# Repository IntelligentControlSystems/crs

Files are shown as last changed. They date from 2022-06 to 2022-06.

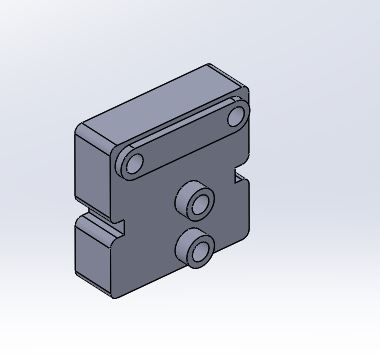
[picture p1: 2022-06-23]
3D_printed_files/miniz_awd/bottom_bracket/Bottom.JPG

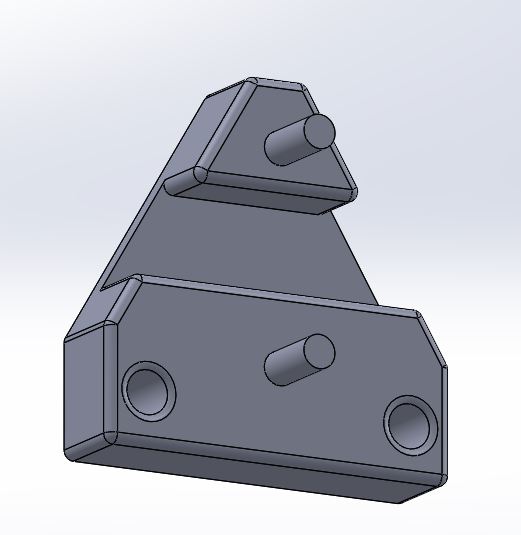
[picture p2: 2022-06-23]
3D_printed_files/assembly_tools/Alignment tool.JPG

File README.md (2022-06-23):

# Collaborative Robotic Systems - CRS


Robotics platform to test control, estimation, and learning algorithms. 

## General 
Collaborative Robotic Systems (CRS) is a flexible and open source hardware and software framework for simulating and testing autonomous racing, autonomous driving, and multi-agent control. This branch contains the hardware design (PCBs, gerber files, BoM, etc).

More information can be found [here](https://idsc.ethz.ch/research-zeilinger/research-projects/demonstrators.html). 

## Contacts
For more information contact [Andrea Carron](https://idsc.ethz.ch/research-zeilinger/research-projects/demonstrators.html)

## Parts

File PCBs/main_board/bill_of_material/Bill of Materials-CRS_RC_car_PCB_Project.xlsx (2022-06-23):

Comment | Description | Designator | Footprint | LibRef | Manufacturer | Manufacturer Part Number | Note | Quantity | Supplier | Supplier Part Number | Library Reference | Manufacturer 1 | Manufacturer Part Number 1 | Supplier 1 | Supplier Part Number 1
22uF | capacitor | C1, C2, C8, C9 | CAP_0603i_1608m -N | Cap |  |  |  | 4 |  |  | Cap |  |  | Digi-Key | 1276-7076-1-ND
2u2F | capacitor | C3, C10 | CAP_0603i_1608m -N | Cap |  |  |  | 2 |  |  | Cap
1nF | capacitor | C4, C13 | CAP_0603i_1608m -N | Cap |  |  |  | 2 |  |  | Cap |  |  | Digi-Key | 478-1215-1-ND
22nF | capacitor | C5, C6, C7, C11, C12, C14 | CAP_0603i_1608m -N | Cap |  |  |  | 6 |  |  | Cap |  |  | Digi-Key | 490-4782-1-ND
0.1uF | capacitor | C15, C18, C20, C21, C34, C35, C39, C41, C42, C51 | CAP_0603i_1608m -N | Cap |  |  |  | 10 |  |  | Cap |  |  | Digi-Key | 1276-1006-1-ND
10nF | capacitor | C16, C36, C38, C47, C48, C49, C50 | CAP_0603i_1608m -N | Cap |  |  |  | 7 |  |  | Cap |  |  | Digi-Key | 399-10040-1-ND
10uF | capacitor | C17, C29 | CAP_0603i_1608m -N | Cap |  |  |  | 2 |  |  | Cap |  |  | Digi-Key | 490-3896-1-ND
1uF | capacitor | C19, C24, C26, C28, C30, C40, C43, C44, C45, C46 | CAP_0603i_1608m -N | Cap |  |  |  | 10 |  |  | Cap |  |  | [NoParam], Digi-Key | [NoParam], 445-1604-1-ND
680pF | capacitor | C22 | CAP_0603i_1608m -N | Cap |  |  |  | 1 |  |  | Cap |  |  | Digi-Key | 478-06035C681JAT2ACT-ND
47uF | capacitor | C23, C31 | CAP_1210i_3225m -N | Cap |  |  |  | 2 |  |  | Cap |  |  | Digi-Key | 490-6538-1-ND
47pF | capacitor | C25, C37 | CAP_0603i_1608m -N | Cap |  |  |  | 2 |  |  | Cap |  |  | Digi-Key | 478-12725-1-ND
10pF | capacitor | C27 | CAP_0603i_1608m -N | Cap |  |  |  | 1 |  |  | Cap |  |  | Digi-Key | 478-1163-1-ND
4.7uF | capacitor | C32, C33 | CAP_0603i_1608m -N | Cap |  |  |  | 2 |  |  | Cap |  |  | Digi-Key | 445-14258-1-ND
4.3nF | capacitor | C52, C53 | CAP_0603i_1608m -N | Cap |  |  |  | 2 |  |  | Cap |  |  | Digi-Key | 311-3858-1-ND
Diode Tranzorb | Transient Voltage Suppression (TVS) Diode | D1 | Diode SMB DO-214aa -N | Diode Tranzorb |  |  |  | 1 |  |  | Diode Tranzorb |  |  | Digi-Key | SMBJ16CALFCT-ND
BZX84J-B12,115 | Schottky Diode | D2, D3, D4, D8 | SOD-323F | Diode Schottky |  |  |  | 4 |  |  | Diode Schottky |  |  | Digi-Key, [NoParam] | 1727-6256-1-ND, [NoParam]
 | LED | D5, D6, D7 | LED_0603i_1608m-n | Diode LED |  |  |  | 3 |  |  | Diode LED
BMI088 Shuttle board 3.0 | Bosch Sensortec BMI088 shuttle board 1.27MM pitch | IC1 | BMI088 Shuttle board 3.0 - SM | BMI088 Shuttle board 3.0 |  |  |  | 1 |  |  | BMI088 Shuttle board 3.0 |  |  | Mouser | 262-SB3.0BMI088
ESP32-WROOM-32D |  | IC2 | ESP32-WROOM-32D | ESP32-WROOM-32D |  |  |  | 1 |  |  | ESP32-WROOM-32D |  |  | Digi-Key | 1904-1023-1-ND
Inductor | Inductor | L1 | Würth 744311470 | Inductor |  |  |  | 1 |  |  | Inductor |  |  | Digi-Key | 732-1153-1-ND
Header 3X2 | Header, 3-Pin, Dual row | P1 | 1.27mm HDR 2X3 THT - KEY | Header 3X2 |  |  |  | 1 |  |  | Header 3X2 |  |  | Mouser | 649-221511-00006T4LF
Tag-Connect TC2050-IDC-NL | 10-pin pogo pin programing port | P3 | TAG-CONNECT TC2050-IDC-NL 10-Pin | Tag-Connect TC2050-IDC-NL-No pin assigned |  |  |  | 1 |  |  | Tag-Connect TC2050-IDC-NL-No pin assigned
5025840970 | 1.50mm Pitch, CLIK-Mate PCB Receptacle, Single Row, Surface Mount, Tin Plating, Positive Lock, 9 Circuits | P4 | CLIK-Mate 1.5mm 9 pin 50258409xx | Molex CLIK-Mate 50258409xx | Molex |  |  | 1 |  |  | Molex CLIK-Mate 50258409xx |  |  | Digi-Key | WM24261CT-ND
JST_SH/SR 3POS 1MM - Side entry | JST SM04B-SRSS-TB same footprint between SR/SZ and SH series | P5, P6, P7, P8, P9 | JST_SH/SR 3POS 1MM - Side entry | JST_SH/SR 3POS 1MM - Side entry | JST | SM03B-SRSS-TB(LF)(SN) |  | 5 |  |  | JST_SH/SR 3POS 1MM - Side entry
MOSFET-P-Power_2 | Power P-Channel MOSFET + pad | Q1, Q2 | PowerPak SO-8 | MOSFET-P-Power_2 |  |  | Check footprint as it may differ | 2 |  |  | MOSFET-P-Power_2 |  |  | Digi-Key, [NoParam] | SI7633DP-T1-GE3CT-ND, [NoParam]
BSS138 | N-Channel MOSFET | Q3, Q4, Q5 | SOT23-N | MOSFET-N | ON Semi. | BSS138 |  | 3 | Digi-Key | BSS138CT-ND | MOSFET-N |  |  | Digi-Key | BSS138NH6327XTSA2CT-ND
10k | Resistor | R1, R11, R23, R31, R35, R36, R39, R42, R44, R54 | RES_0603i_1608m -N | Res |  |  |  | 10 |  |  | Res |  |  | [NoParam], Digi-Key | [NoParam], RMCF0603FT10K0CT-ND
18k | Resistor | R2, R12, R62 | RES_0603i_1608m -N | Res |  |  |  | 3 |  |  | Res |  |  | Digi-Key | P18.0KHCT-ND
22k | Resistor | R3, R13 | RES_0603i_1608m -N | Res |  |  |  | 2 |  |  | Res |  |  | Digi-Key | 311-22KDCT-ND
4.42k | Resistor | R4 | RES_0603i_1608m -N | Res |  |  |  | 1 |  |  | Res |  |  | Digi-Key | 311-2376-1-ND
1.6 | Resistor | R5, R6, R7, R8, R15, R16, R17, R18 | RES_0603i_1608m -N | Res |  |  |  | 8 |  |  | Res |  |  | Mouser | 667-ERJ-3BQF1R6V
1k | Resistor | R9, R19, R21, R22, R24, R27, R29, R38 | RES_0603i_1608m -N | Res |  |  |  | 8 |  |  | Res |  |  | Digi-Key, [NoParam] | 311-1.00KHRCT-ND, [NoParam], 2019-RK73H1JTTD1001FCT-ND
47k | Resistor | R10, R20, R41 | RES_0603i_1608m -N | Res |  |  |  | 3 |  |  | Res |  |  | Digi-Key, [NoParam] | A103102CT-ND, [NoParam], P42.2KCCT-ND
2.32k | Resistor | R14 | RES_0603i_1608m -N | Res |  |  |  | 1 |  |  | Res |  |  | Digi-Key | P20322CT-ND
0Ohm | Resistor | R25, R57, R58, R59, R60 | RES_0603i_1608m -N | Res |  |  |  | 5 |  |  | Res |  |  | Digi-Key, [NoParam] | CR0603-J/-000ELFCT-ND, [NoParam]
330R | Resistor | R26, R28 | RES_0603_1608m -L | Res |  |  | 1%, <100ppm/K, 0.1W | 2 |  |  | Res |  |  | Digi-Key | 311-33.0HRCT-ND
1.4k | Resistor | R30, R48, R49, R55 | RES_0603i_1608m -N | Res |  |  |  | 4 |  |  | Res |  |  | [NoParam], Digi-Key | [NoParam], P1.4KDBCT-ND
1M | Resistor | R32, R37 | RES_0603i_1608m -N | Res |  |  |  | 2 |  |  | Res |  |  | Digi-Key | 311-1.00MHRCT-ND
845k | Resistor | R33 | RES_0603i_1608m -N | Res |  |  |  | 1 |  |  | Res |  |  | Digi-Key | 311-845KHRCT-ND
33k | Resistor | R34 | RES_0603i_1608m -N | Res |  |  |  | 1 |  |  | Res |  |  | Digi-Key | A129706CT-ND
143k | Resistor | R40 | RES_0603i_1608m -N | Res |  |  |  | 1 |  |  | Res |  |  | Digi-Key | 311-2425-1-ND
100k | Resistor | R43, R52 | RES_0603i_1608m -N | Res |  |  |  | 2 |  |  | Res
499k 0.1% | Resistor | R45, R46 | RES_0603i_1608m -N | Res |  |  |  | 2 |  |  | Res |  |  | Digi-Key | 1712-RP73D1J499KBTDFCT-ND
110k 0.1% | Resistor | R47 | RES_0603i_1608m -N | Res |  |  |  | 1 |  |  | Res |  |  | Digi-Key | A139989CT-ND
100 | Resistor | R50, R56 | RES_0603i_1608m -N | Res |  |  |  | 2 |  |  | Res
10 | Resistor | R51 | RES_0603i_1608m -N | Res |  |  |  | 1 |  |  | Res
NP | Resistor | R53 | RES_0603i_1608m -N | Res |  |  |  | 1 |  |  | Res
SW SPDT | Single-Pole, Double-Throw Switch | S1 | WS-SLS | SW SPDT |  |  |  | 1 |  |  | SW SPDT |  |  | Digi-Key | 732-13665-1-ND
SW PB | Switch | S2, S3, S4 | WS-TASV | SW PB |  |  |  | 3 |  |  | SW PB |  |  | Digi-Key | 732-7039-1-ND
STSPIN250 | H-Bridged Brush DC Motor Driver, Single, Low-Voltage | U1, U2 | VFQFPN16_M | STSPIN250 | STMicroelectronics |  |  | 2 | [NoParam], DigiKey | [NoParam], 497-17035-1-ND | STSPIN250 |  |  | Digi-Key | 497-17035-1-ND
LTC3112 | DC/DC Converter: Reg Buck/Boost Adj 2.5A | U3 | TSSOP-20_ExposedPad | LTC3112 |  |  |  | 1 |  |  | LTC3112 |  |  | Digi-Key | LTC3112IFE#PBF-ND
AP2115M-3.3TRG1 | Linear Voltage Regulator IC Positive Fixed 1 Output 1A 8-SOIC 3.3V | U4 | SOIC-8 | AP2115M-3.3TRG1 |  |  |  | 1 |  |  | AP2115M-3.3TRG1 |  |  | Digi-Key | AP2115M-3.3TRG1DICT-ND
LMV358QDDUR | General Purpose Amplifier 2 Circuit Rail-to-Rail 8-VSSOP | U5 | 8-VFSOP (0.091", 2.30mm Width) | LMV358QDDUR |  |  |  | 1 |  |  | LMV358QDDUR
TLV6713 | Voltage comparator | U6 | SOT23-6-N | TLV6713 |  |  | WINDOW COMPARATOR | 1 |  |  | TLV6713 |  |  | Digi-Key | 296-51699-1-ND
NB: this pinout is only true for the UFQFPN32 model!! | ARM Cortex-M0+ series Microcontroller IC 32-Bit 32MHz 16KB (16K x 8) FLASH | U7 | QFN50P500X500X60_HS-33N | STM32L011K4U6 | STMicroelectronics |  |  | 1 | Digi-Key | 497-19188-ND | STM32L011K4U6
SN74LV1T34 | Single Power Supply Single Buffer GATE CMOS Logic Level Shifter | U8, U9 | SOT23-5-N | SN74LV1T34 | Texas Instruments | SN74LV1T34DBVR |  | 2 | Digi-Key | 296-37176-1-ND | SN74LV1T34 |  |  | TI store | SN74LV1T34DBVR
Jumper | Jumper Wire | W1 | RES_0603i_1608m -N | Jumper |  |  |  | 1 |  |  | Jumper
32768Hz | Crystal Oscillator | Y1 | ECX-12RR | XTAL2 |  |  |  | 1 |  |  | XTAL2 |  |  | Digi-Key | XC3096CT-ND

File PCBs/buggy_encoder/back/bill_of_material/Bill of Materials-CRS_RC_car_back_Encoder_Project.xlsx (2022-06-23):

Comment | Description | Designator | Footprint | LibRef | Manufacturer | Manufacturer Part Number | Note | Quantity | Supplier | Supplier Part Number | Library Reference
0.1uF | capacitor | C1, C2 | CAP_0603i_1608m -N | Cap |  |  |  | 2 |  |  | Cap
Header 3 | Header, 3-Pin | P1 | 1.27mm HDR1X3 | Header 3 |  |  |  | 1 |  |  | Header 3
TMAG5123D1CQ | Board Mount Hall Effect/Magnetic Sensors High-voltage (up to 38 V), in-plane, high-precision switch | U1, U2 | SOT23-N | TMAG5123D1CQ |  |  |  | 2 |  |  | TMAG5123D1CQ

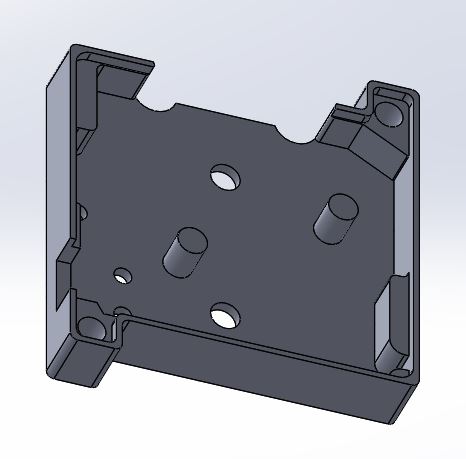
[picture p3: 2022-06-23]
3D_printed_files/common_parts/All three models/Top PCB bracket/Top bracket.JPG

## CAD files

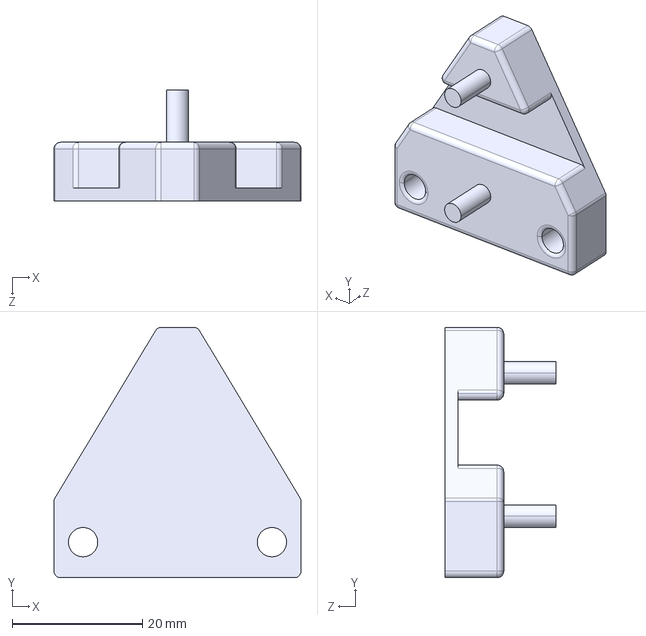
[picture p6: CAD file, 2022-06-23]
3D_printed_files/assembly_tools/Alignment tool buggy bracket.STEP
37.9 x 38.5 x 17.0 mm

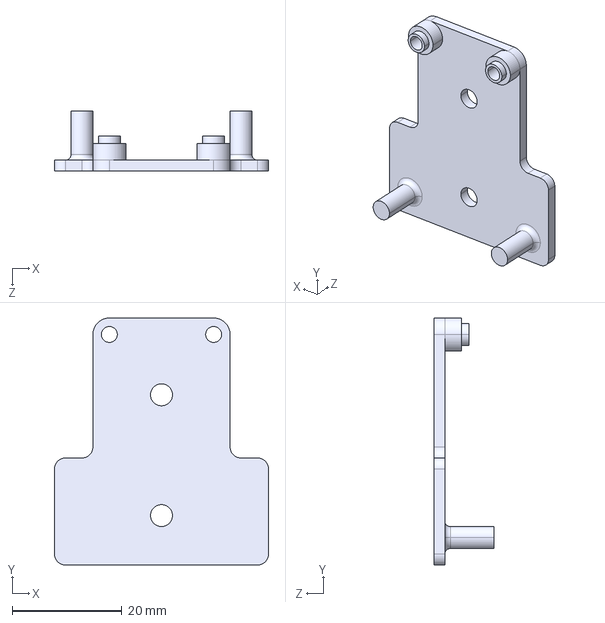
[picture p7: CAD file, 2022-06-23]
3D_printed_files/buggy/Bottom bracket/Bottom bracket.STEP
39.0 x 45.0 x 11.0 mm

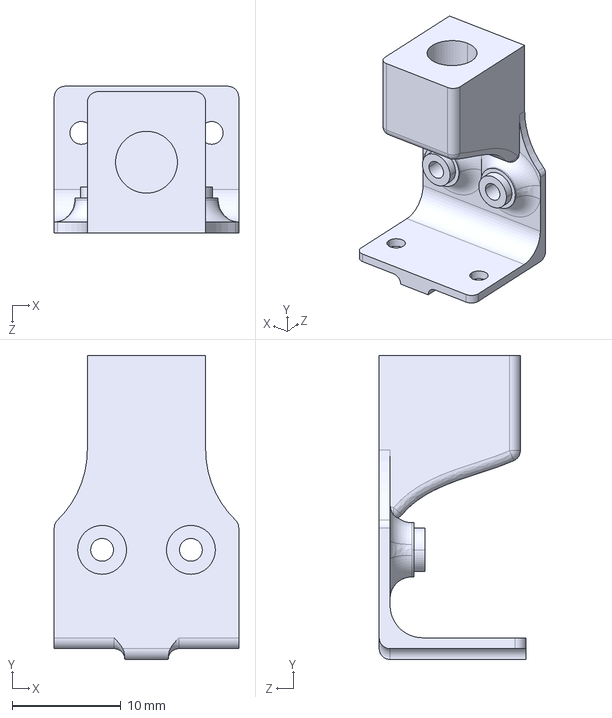
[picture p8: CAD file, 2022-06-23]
3D_printed_files/buggy/Vicon marker bracket/Buggy vicon bracket front.STEP
17.0 x 28.0 x 13.5 mm

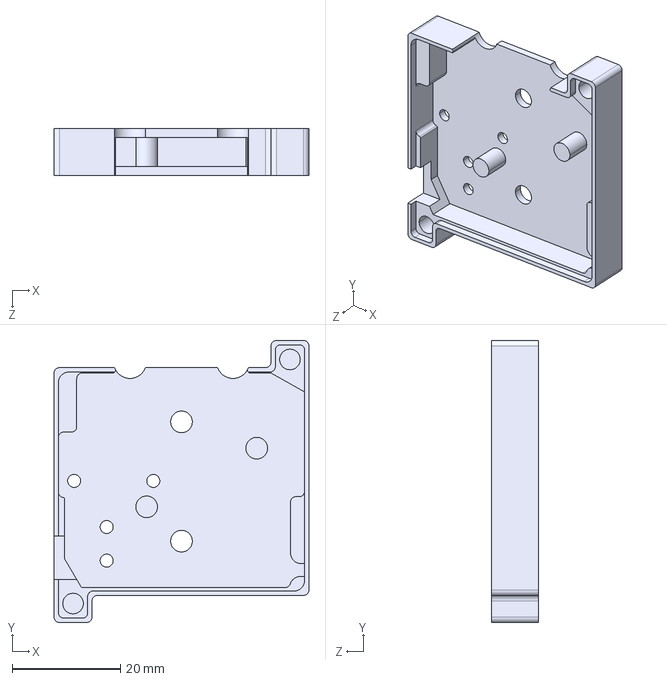
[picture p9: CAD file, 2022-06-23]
3D_printed_files/common_parts/All three models/Top PCB bracket/Top bracket.STEP
47.0 x 52.0 x 8.59 mm

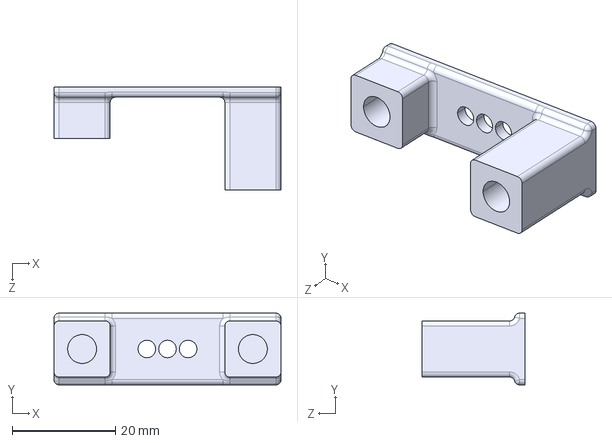
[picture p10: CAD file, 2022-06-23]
3D_printed_files/common_parts/All three models/Vicon top bracket/Vicon top bracket.STEP
44.0 x 13.9 x 20.0 mm

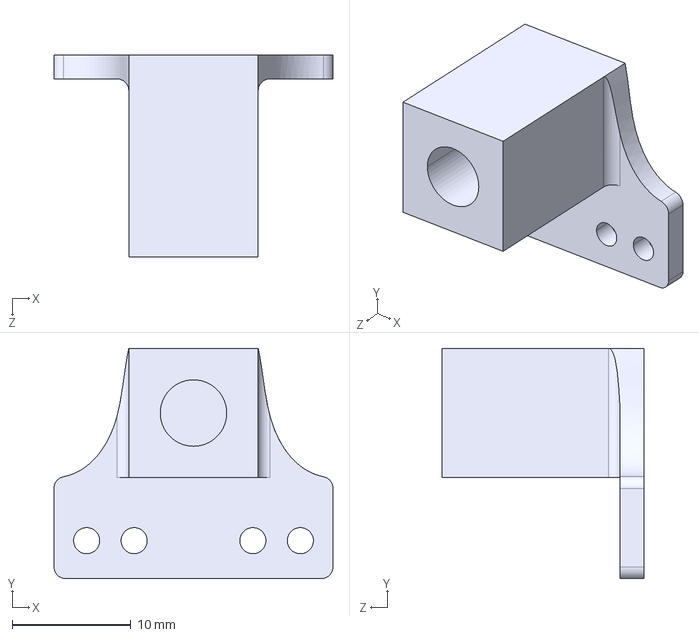
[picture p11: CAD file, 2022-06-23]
3D_printed_files/common_parts/Mini z AWD and Mini z RWD/Vicon bracket/Mini z AWD ball bracket front.STEP
23.5 x 19.4 x 17.0 mm

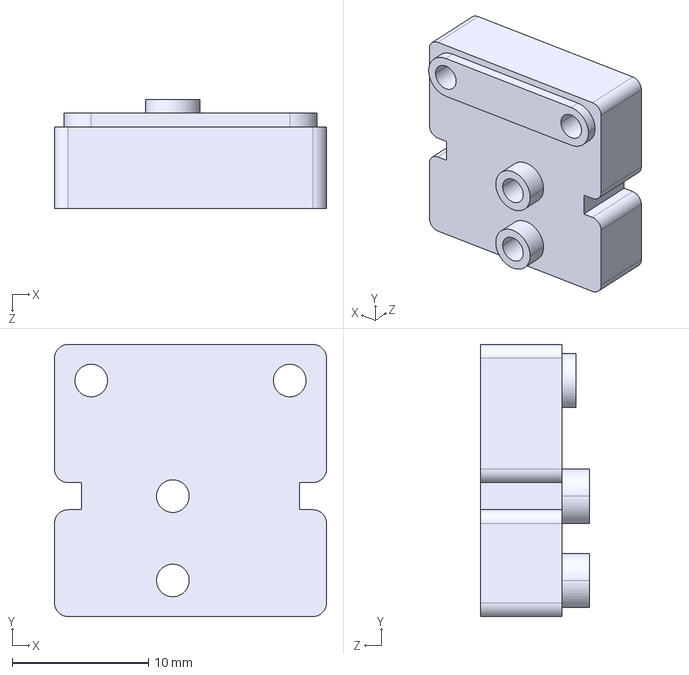
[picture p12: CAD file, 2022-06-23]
3D_printed_files/miniz_awd/bottom_bracket/Bottom bracket mini z AWD.STEP
20.0 x 20.0 x 8.00 mm

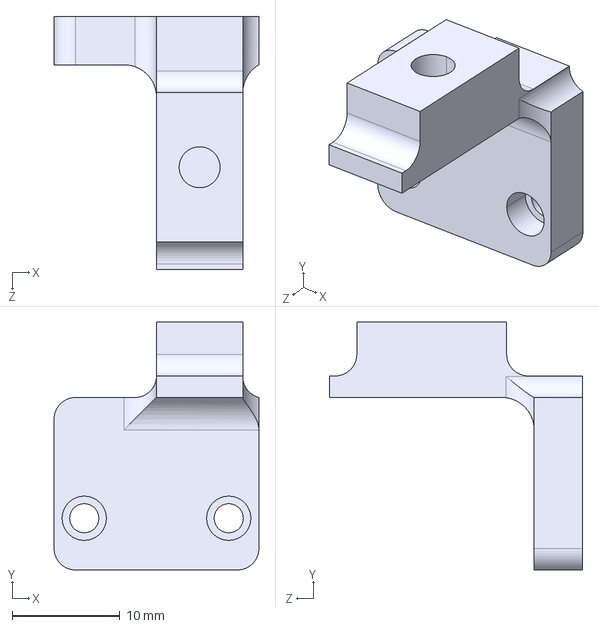
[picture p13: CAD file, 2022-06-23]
3D_printed_files/miniz_awd/vicon_bracket/Miniz AWD bracket back bottom.STEP
19.0 x 23.0 x 23.5 mm

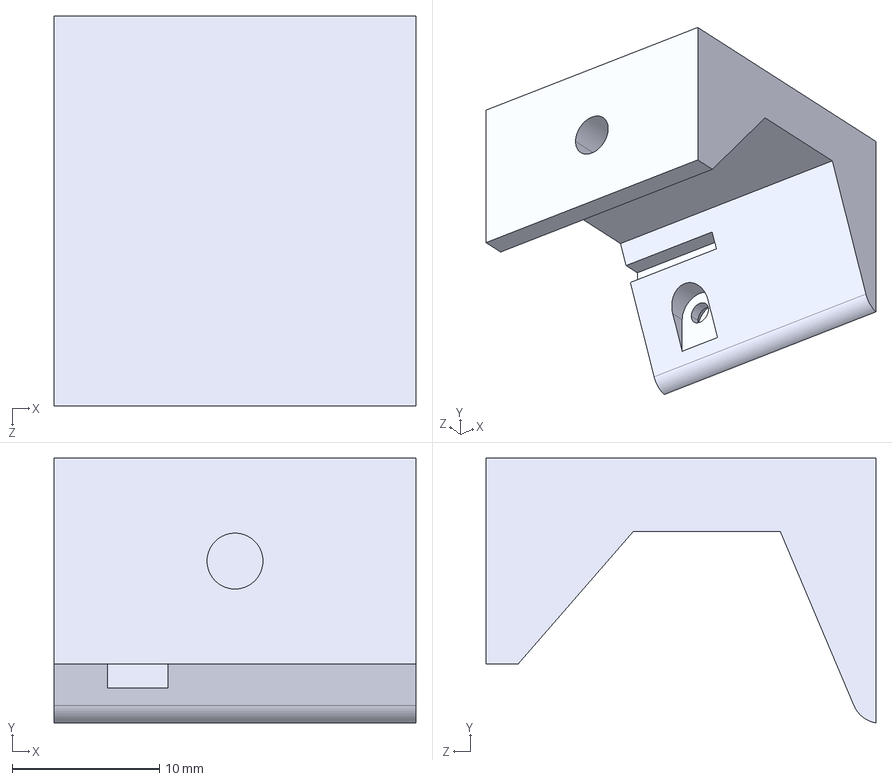
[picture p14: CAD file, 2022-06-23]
3D_printed_files/miniz_rwd/vicon_bracket/Mini z RWD vicon ball mount back.STEP
24.6 x 18.0 x 26.5 mm

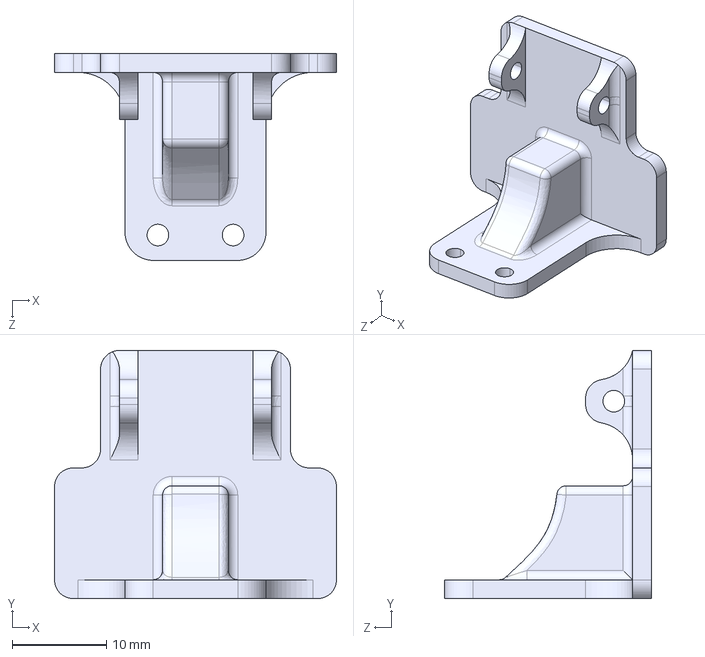
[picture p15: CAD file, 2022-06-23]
3D_printed_files/buggy/Vicon marker bracket/Buggy vicon back bracket bottom.STEP
30.0 x 26.4 x 22.0 mm

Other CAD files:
3D_printed_files/miniz_rwd/bottom_bracket/Bottom plate Mini z RWD.STEP
3D_printed_files/assembly_tools/Alignment tool buggy bracket.STL
3D_printed_files/buggy/Bottom bracket/Bottom bracket.STL
3D_printed_files/buggy/Vicon marker bracket/Buggy vicon back bracket bottom.STL
3D_printed_files/buggy/Vicon marker bracket/Buggy vicon bracket front.STL
3D_printed_files/common_parts/All three models/Top PCB bracket/Top bracket.STL
3D_printed_files/common_parts/All three models/Vicon top bracket/Vicon top bracket.STL
3D_printed_files/common_parts/Mini z AWD and Mini z RWD/Vicon bracket/Mini z AWD ball bracket front.STL
3D_printed_files/miniz_awd/bottom_bracket/Bottom bracket mini z AWD.STL
3D_printed_files/miniz_awd/vicon_bracket/Miniz AWD bracket back bottom.STL
3D_printed_files/miniz_rwd/bottom_bracket/Bottom plate Mini z RWD.STL
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

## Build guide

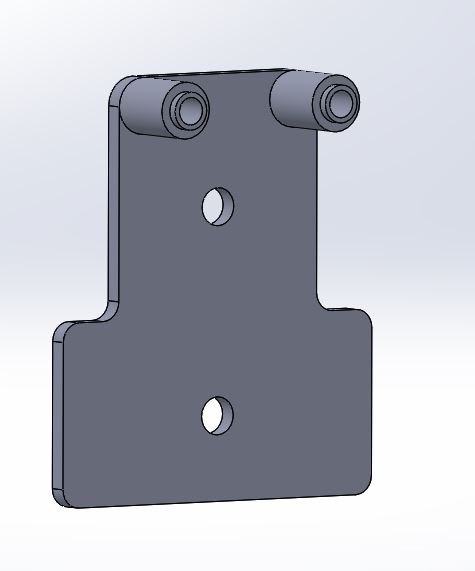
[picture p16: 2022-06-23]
3D_printed_files/miniz_rwd/bottom_bracket/Bottom.JPG

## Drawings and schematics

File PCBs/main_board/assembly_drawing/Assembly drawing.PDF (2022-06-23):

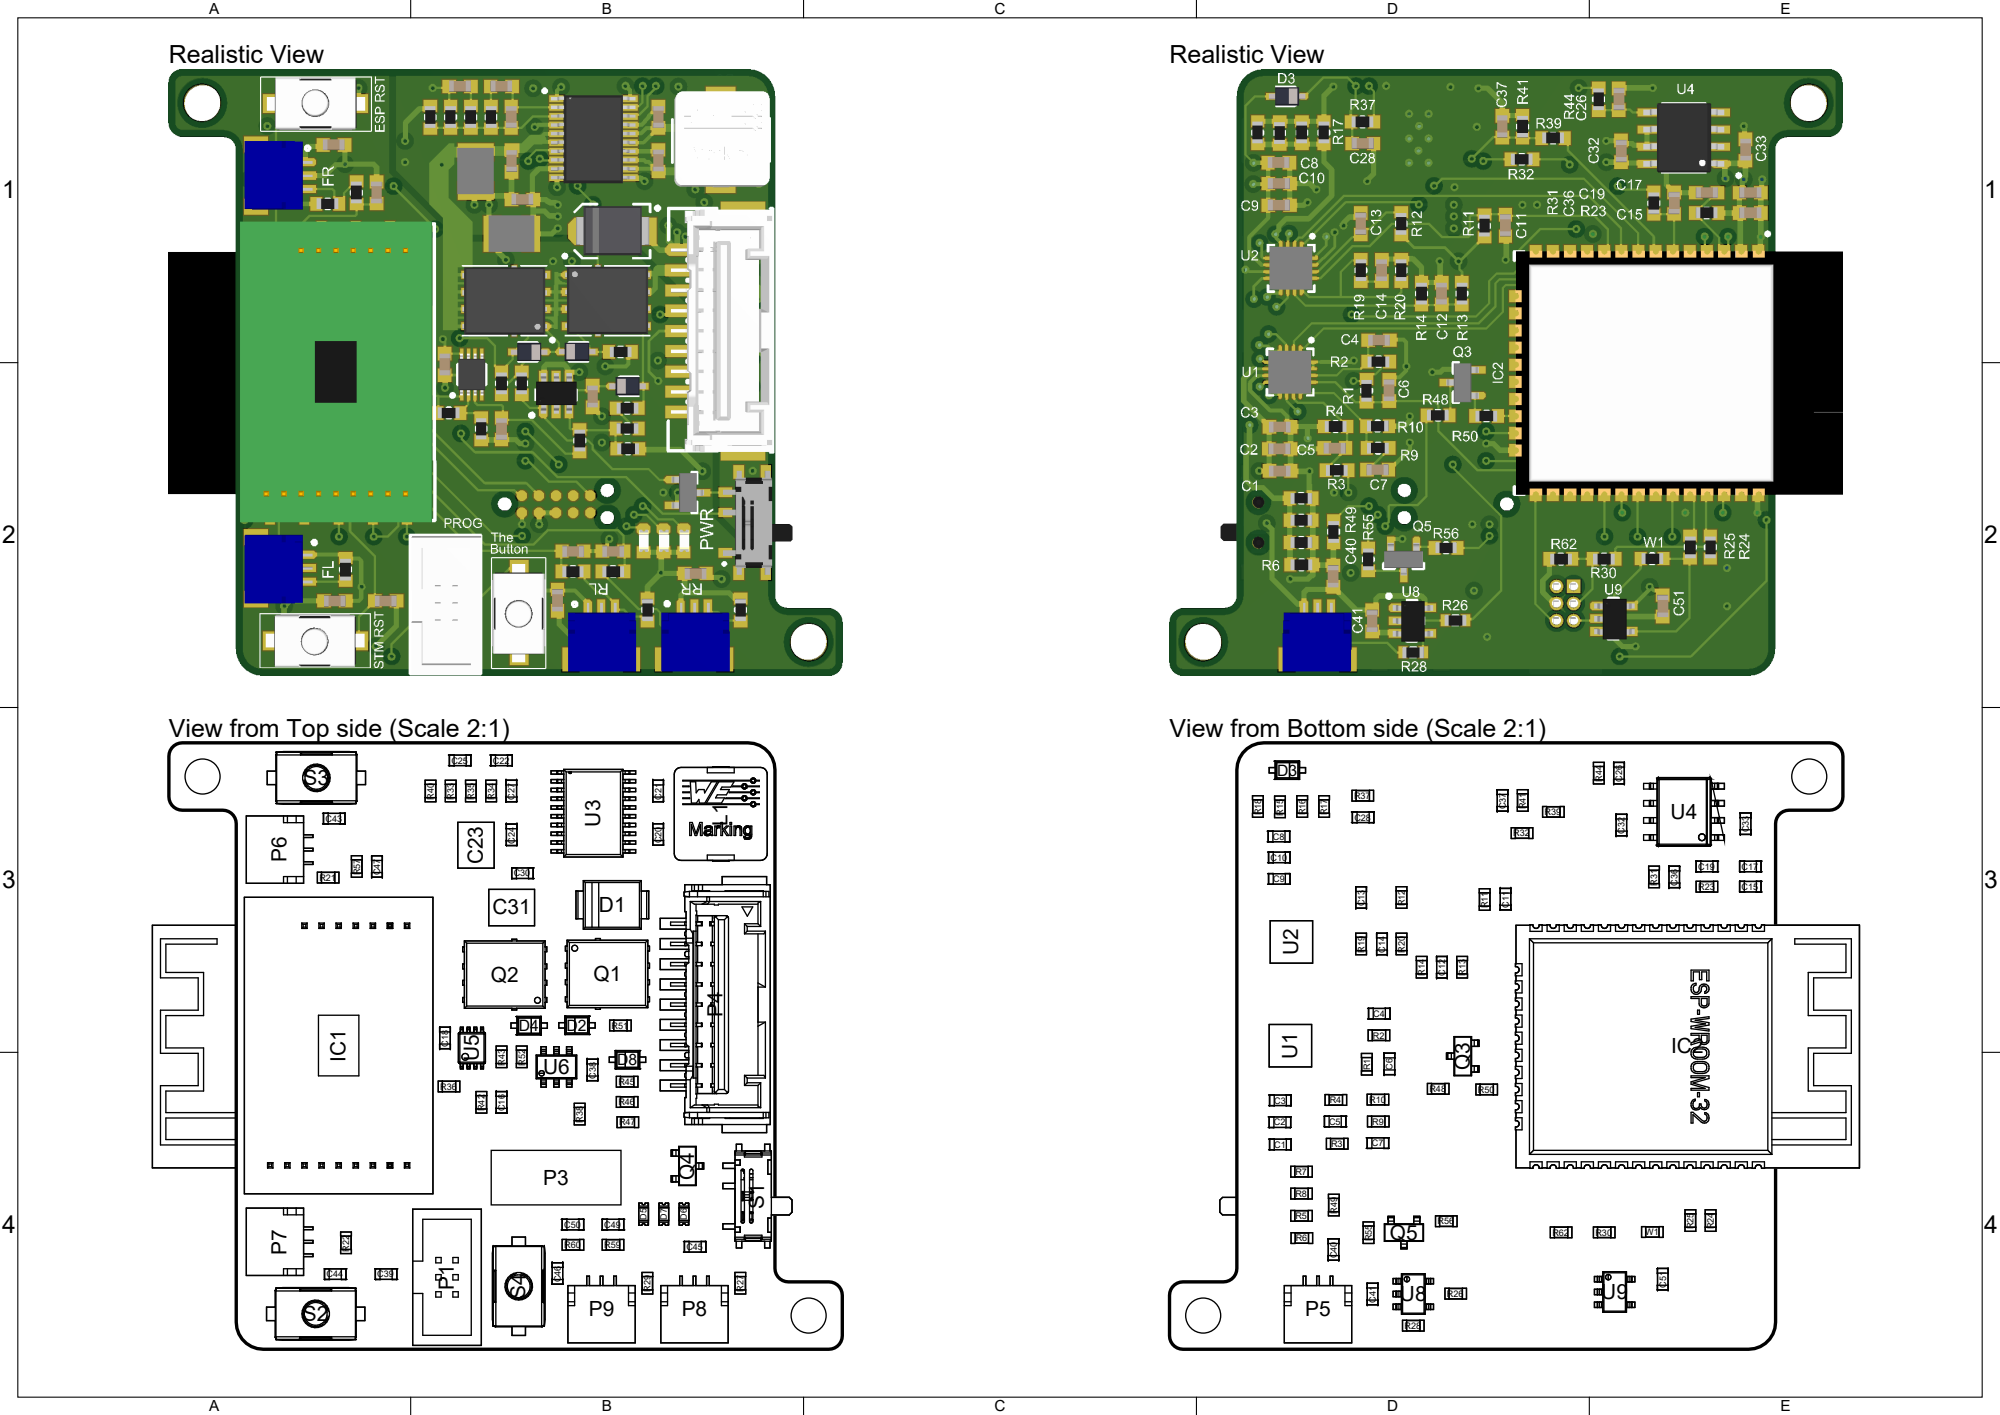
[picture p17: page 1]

View from Top side (Scale 2:1)

View from Bottom side (Scale 2:1)

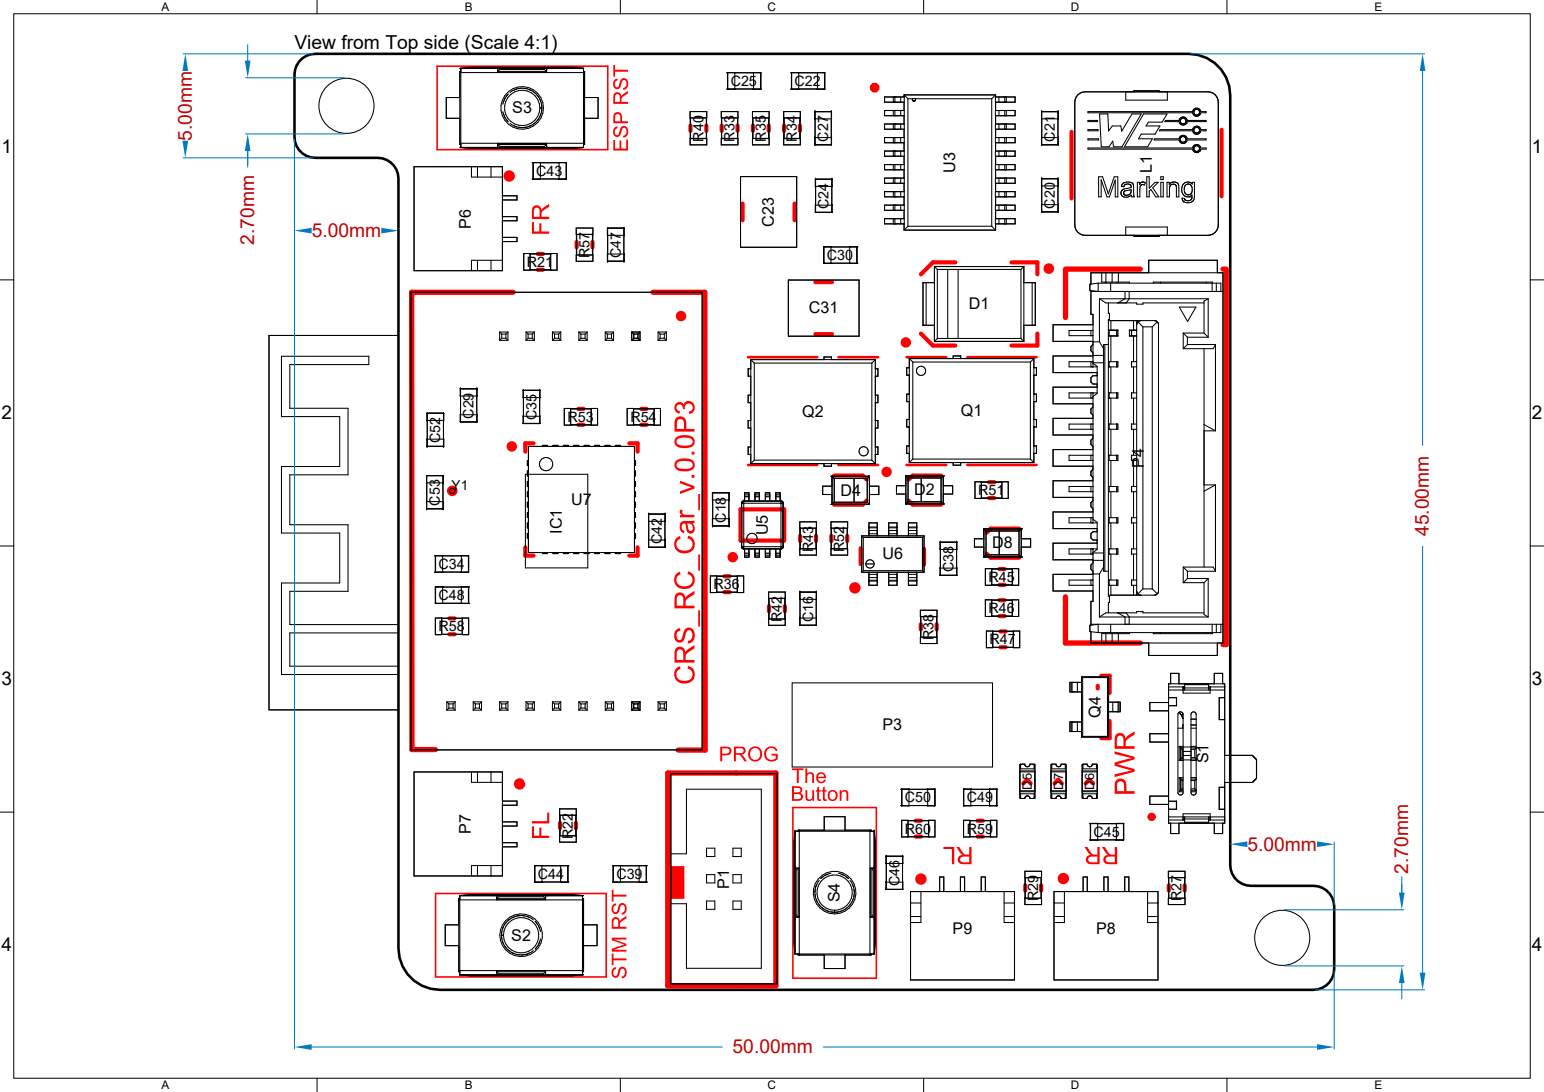
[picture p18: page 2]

View from Top side (Scale 4:1)

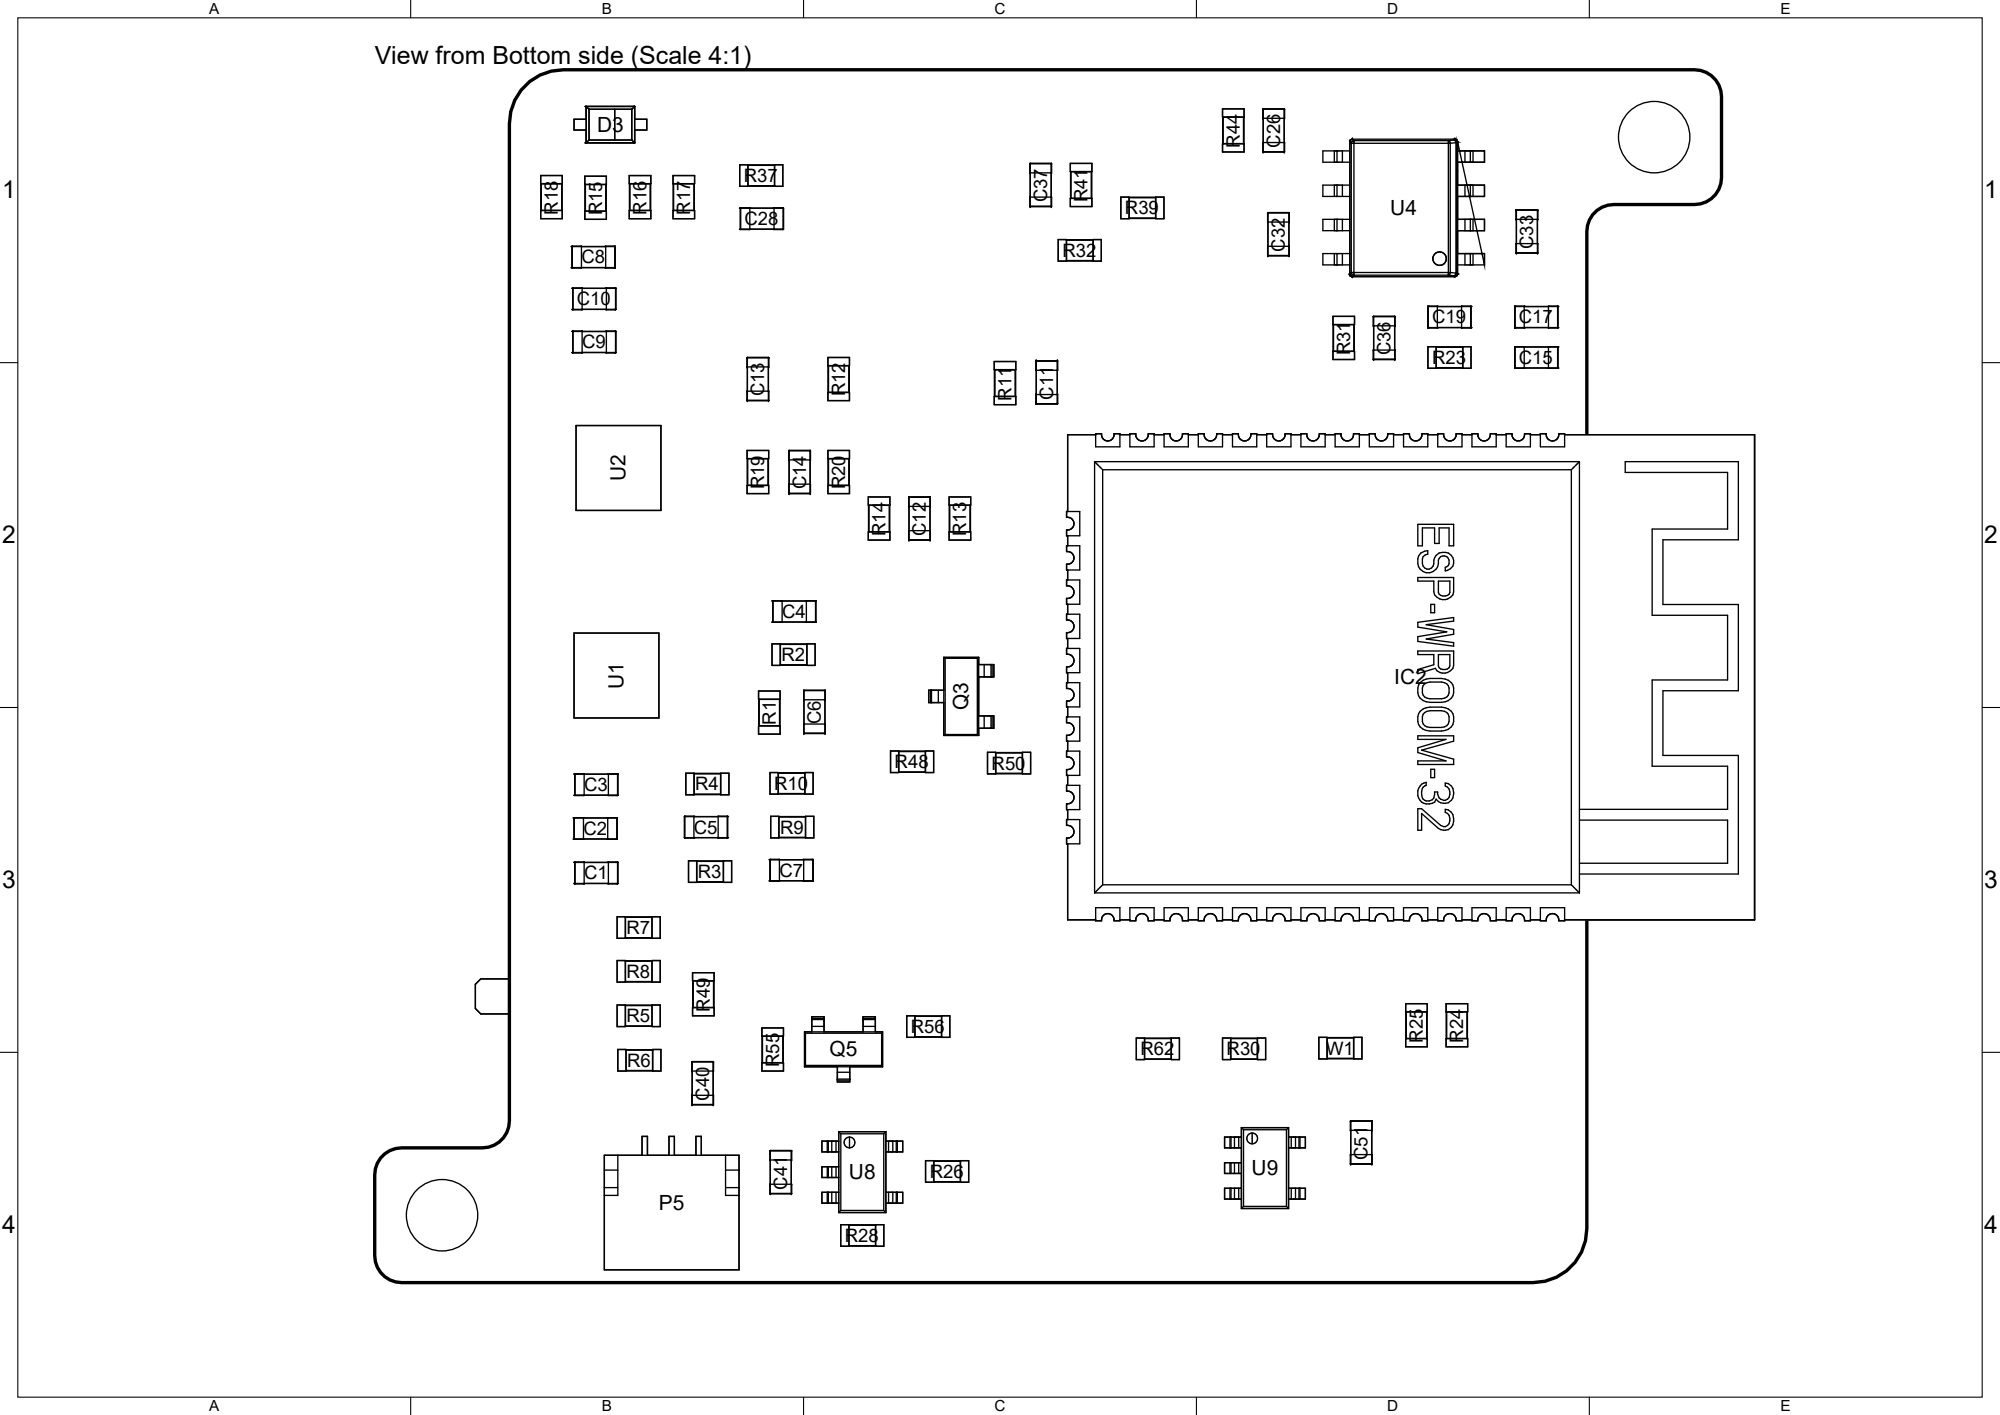
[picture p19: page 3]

View from Bottom side (Scale 4:1)

1 | 1
2 | 2
3 | 3
4 | 4
Material | Layer | Thickness Dielectric Material Type | Gerber
| Top Overlay | | Legend | GTO
Surface Material Top Solder | 0.010mm Solder Resist | Solder Mask | GTS
Copper | Top Layer | 0.036mm | Signal | GTL
Prepreg | | 0.200mm PP-006 | Dielectric
CF-004 | Power | 0.018mm | Internal Plane GP1
1.065mm FR-4 | Dielectric
CF-004 | GND | 0.018mm | Internal Plane GP2
Prepreg | 0.200mm PP-006 | Dielectric
Copper | Bottom Layer 0.036mm | Signal | GBL
Surface Material Bottom Solder 0.010mm Solder Resist | Solder Mask | GBS
Bottom Overlay | Legend | GBO
Total thickness: 1.591mm

Layer Stack Legend

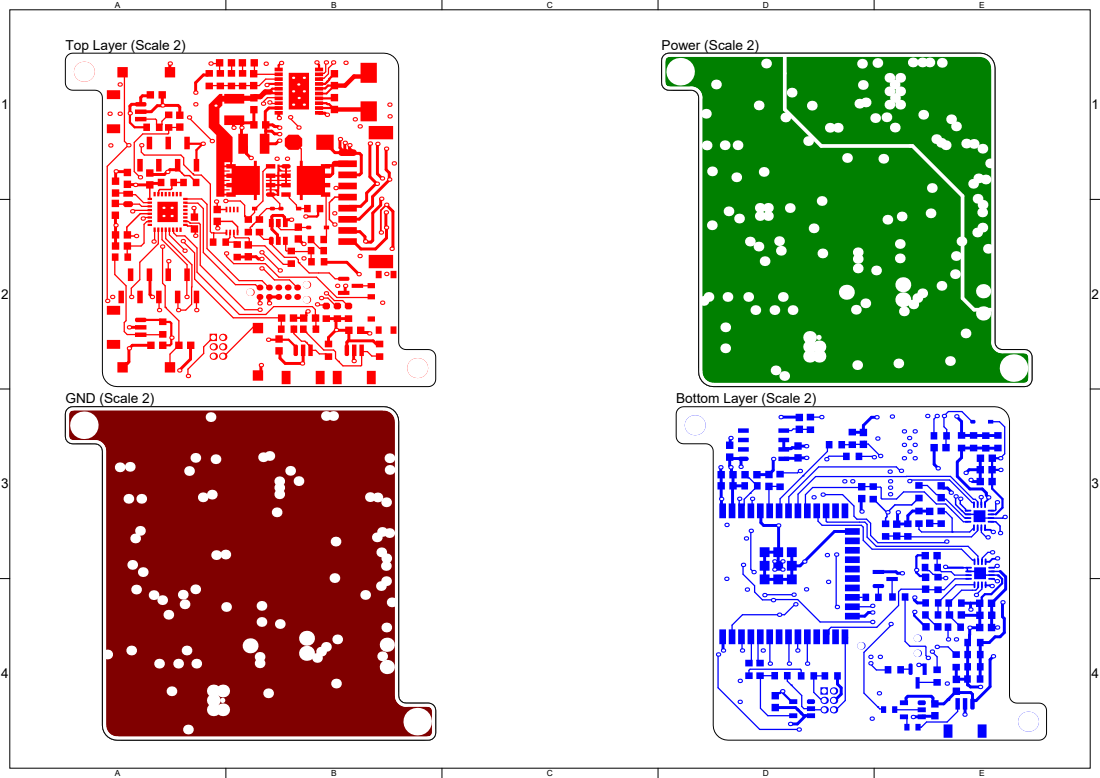
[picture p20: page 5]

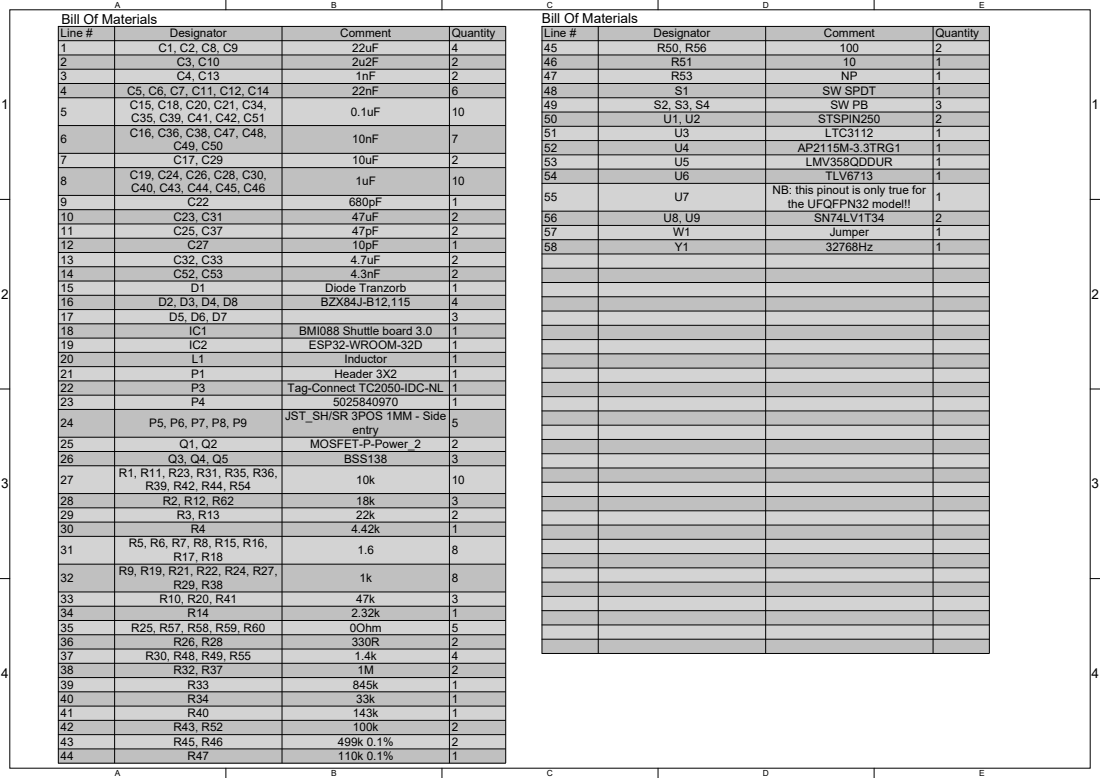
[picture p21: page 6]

55 | U7 | NB: this pinout is only true for the UFQFPN32 model!!

15 | D1 | Diode Tranzorb
16 | D2, D3, D4, D8 | BZX84J-B12,115
17 | D5, D6, D7
18 | IC1 | BMI088 Shuttle board 3.0
19 | IC2 | ESP32-WROOM-32D
20 | L1 | Inductor
21 | P1 | Header 3X2
22 | P3 | Tag-Connect TC2050-IDC-NL
23 | P4 | 5025840970
24 | P5, P6, P7, P8, P9 | JST_SH/SR 3POS 1MM - Side entry

25 | Q1, Q2 | MOSFET-P-Power_2
26 | Q3, Q4, Q5 | BSS138
27 | R1, R11, R23, R31, R35, R36, R39, R42, R44, R54 | 10k
32 | R9, R19, R21, R22, R24, R27, R29, R38 | 1k | 1032188315242111221
28 | R2, R12, R62 | 18k
29 | R3, R13 | 22k
30 | R4 | 4.42k
31 | R5, R6, R7, R8, R15, R16, R17, R18 | 1.6

33 | R10, R20, R41 | 47k
34 | R14 | 2.32k
35 | R25, R57, R58, R59, R60 | 0Ohm
36 | R26, R28 | 330R
37 | R30, R48, R49, R55 | 1.4k
38 | R32, R37 | 1M
39 | R33 | 845k
40 | R34 | 33k
41 | R40 | 143k
42 | R43, R52 | 100k
43 | R45, R46 | 499k 0.1%
44 | R47 | 110k 0.1%

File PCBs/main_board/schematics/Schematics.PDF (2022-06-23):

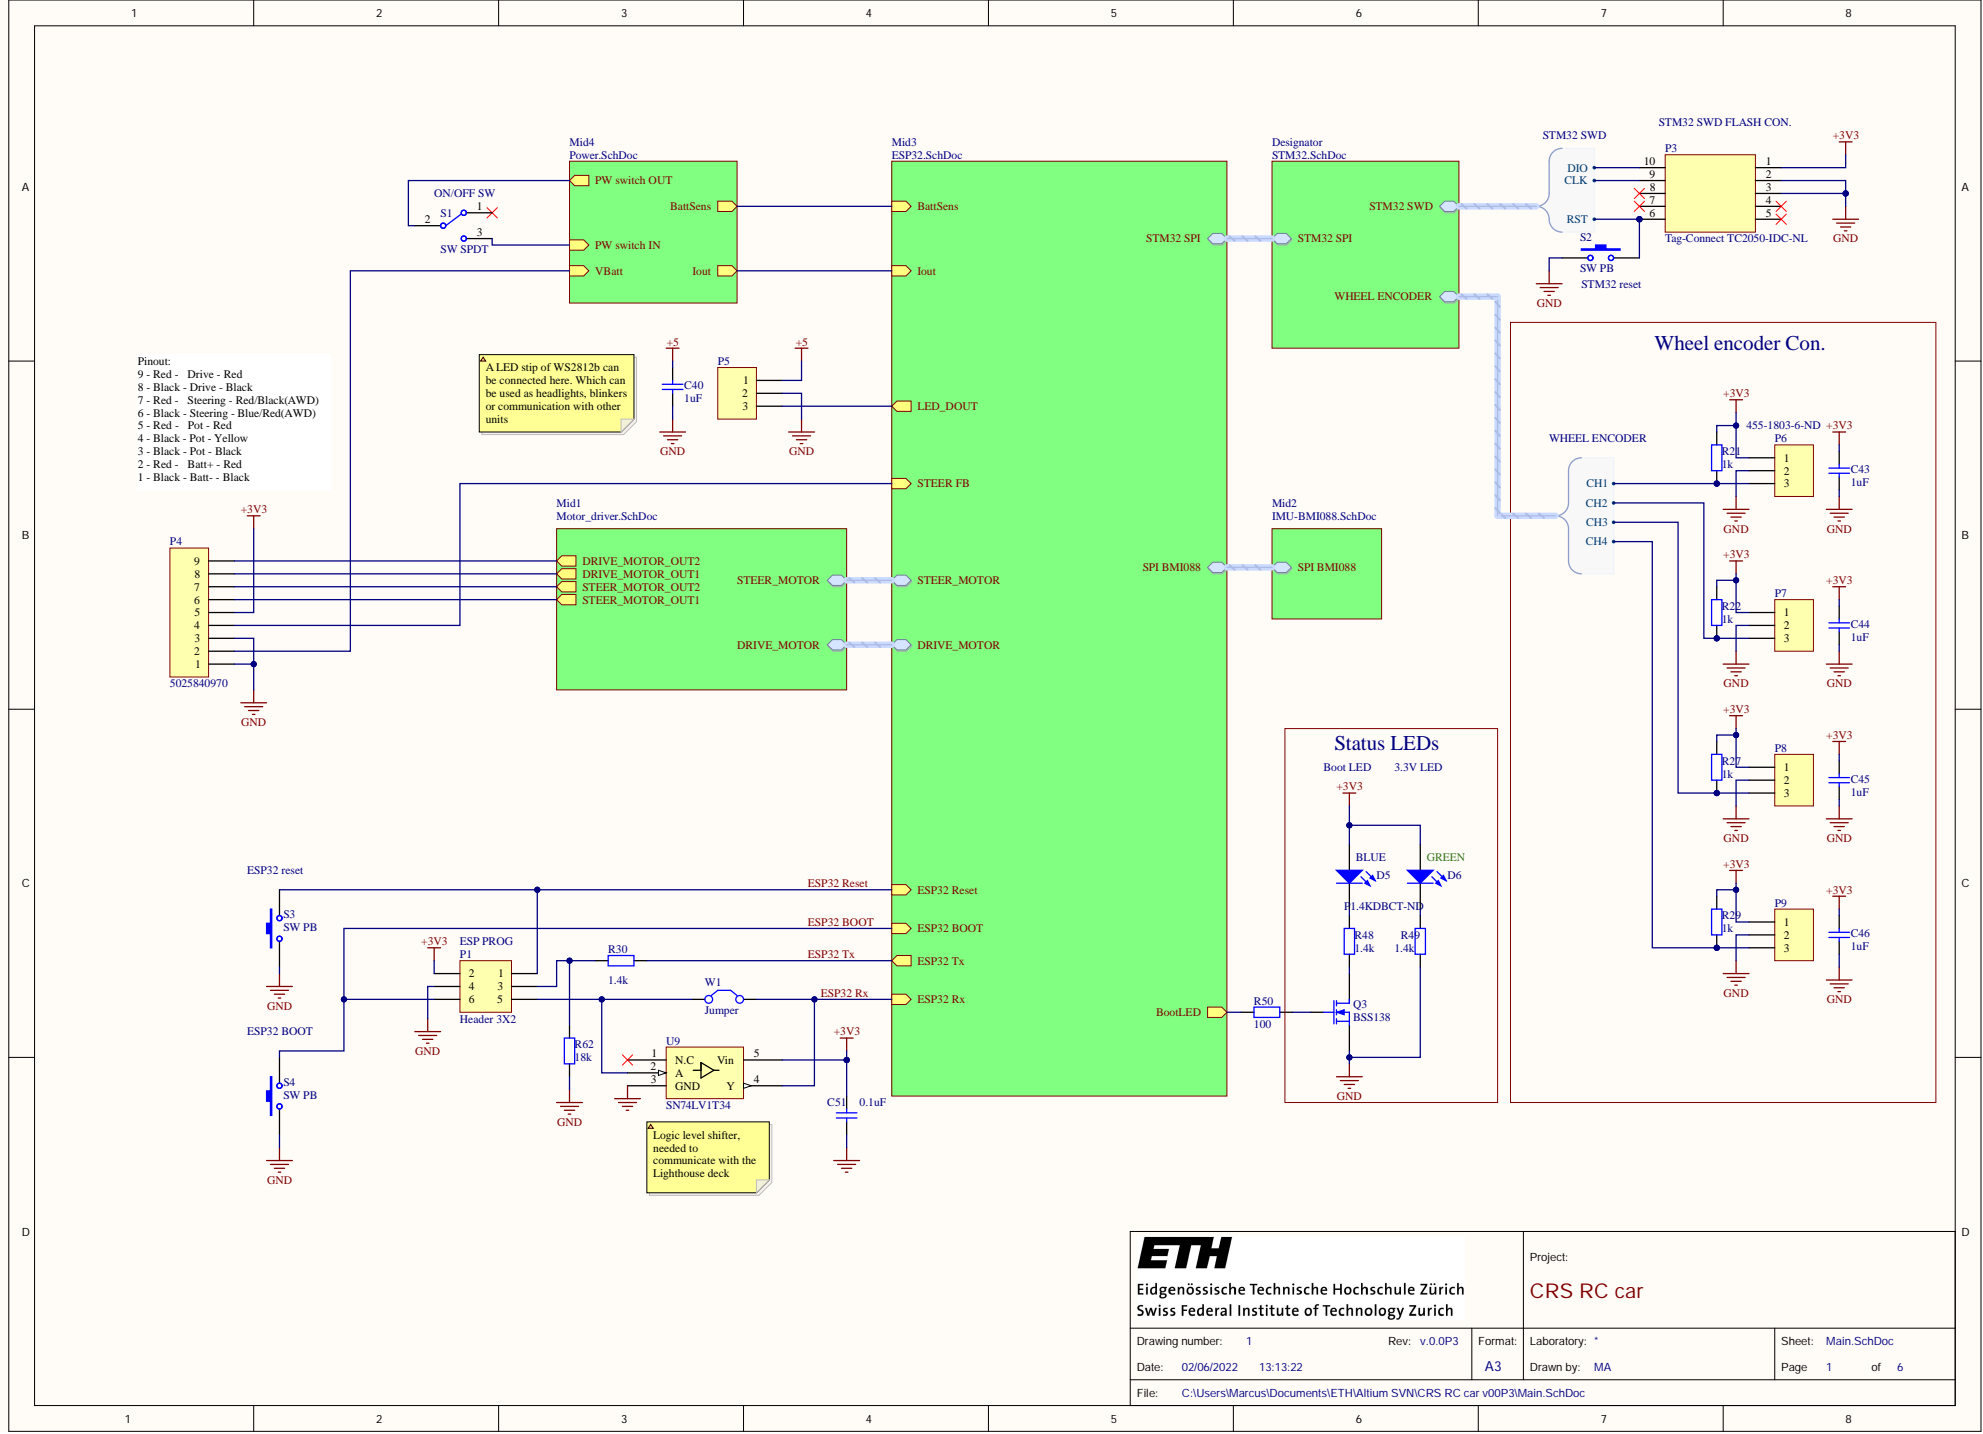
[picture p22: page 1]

Pinout:
9 - Red - Drive - Red
8 - Black - Drive - Black
7 - Red - Steering - Red/Black(AWD)
6 - Black - Steering - Blue/Red(AWD)
5 - Red - Pot - Red
4 - Black - Pot - Yellow
3 - Black - Pot - Black
2 - Red - Batt+ - Red
1 - Black - Batt- - Black

A LED stip of WS2812b can
be connected here. Which can
be used as headlights, blinkers
or com
units

ESP32 BOOT

+3V3 ES P PROG | R30

Project: CRS R C c a r

Drawing number: Rev: v.0.0P3 Date: 13:13:22 | Format: A3 | Laboratory: * Drawn by: MA | Sheet: Main.SchDoc Page 1 of

C:\Users\Marcus\Documents\ETH\Altium SVN\CRS RC car v00P3\Main.SchDoc

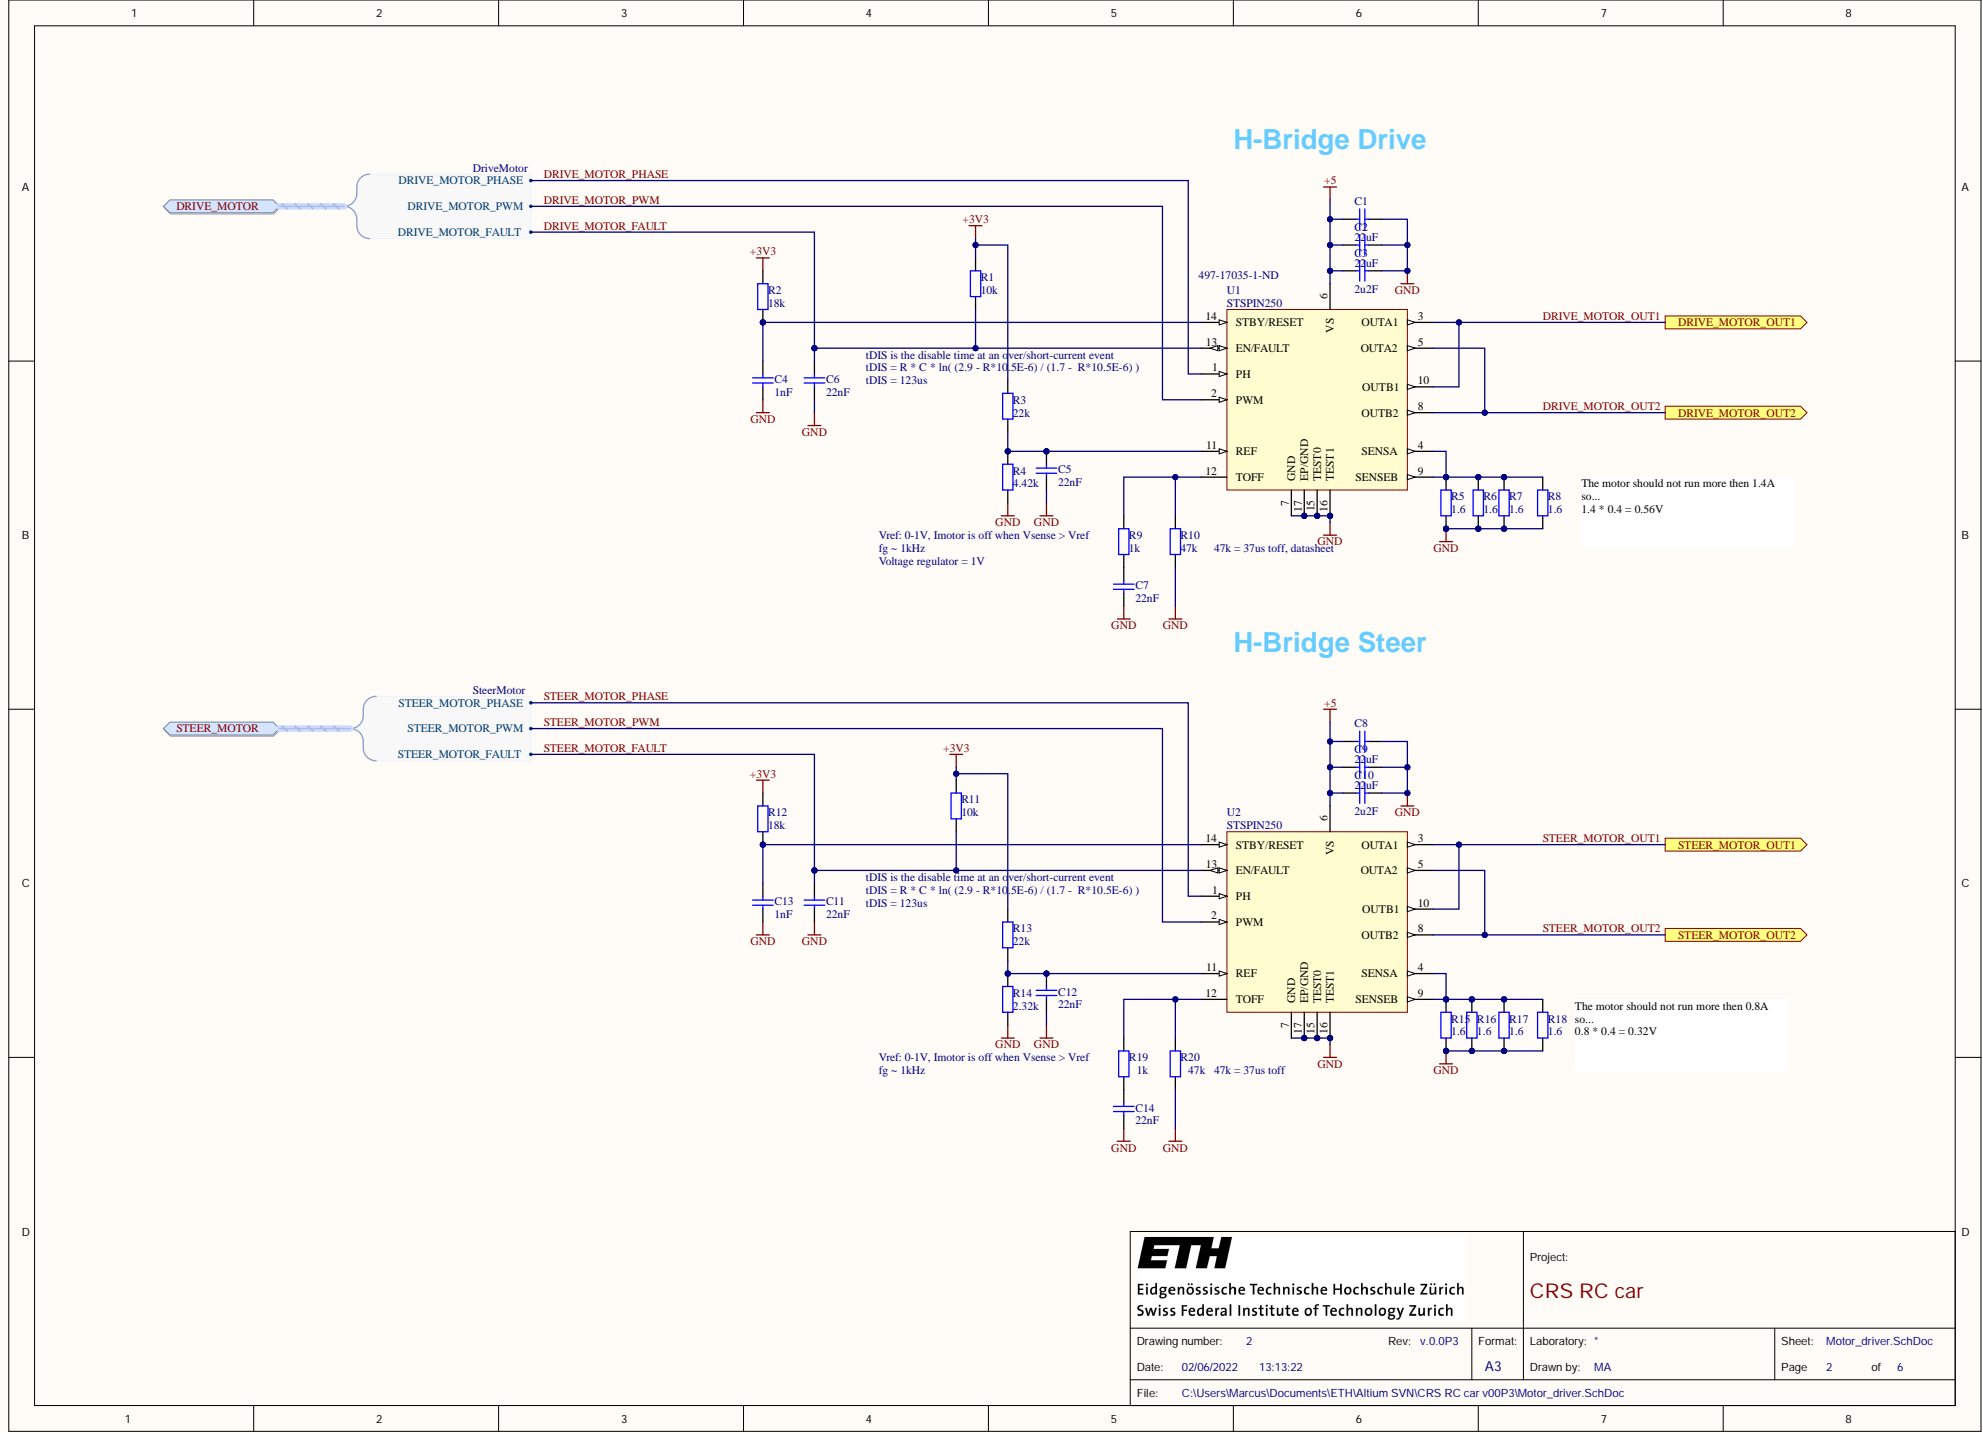
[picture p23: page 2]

S is the disable time at an over/short-current event

tDI S = R * C * ln( (2.9 - R*10.5E-6) / (1.7 - R*10.5E-6) )

The motor should not run more then 1.4A

motor is off when Vsense > Vref

The motor should not run more then 0.8A

Project: CRS R C c a r

Motor_driver.SchDoc

C:\Users\Marcus\Documents\ETH\Altium SVN\CRS RC car v00P3\Motor_driver.SchDoc

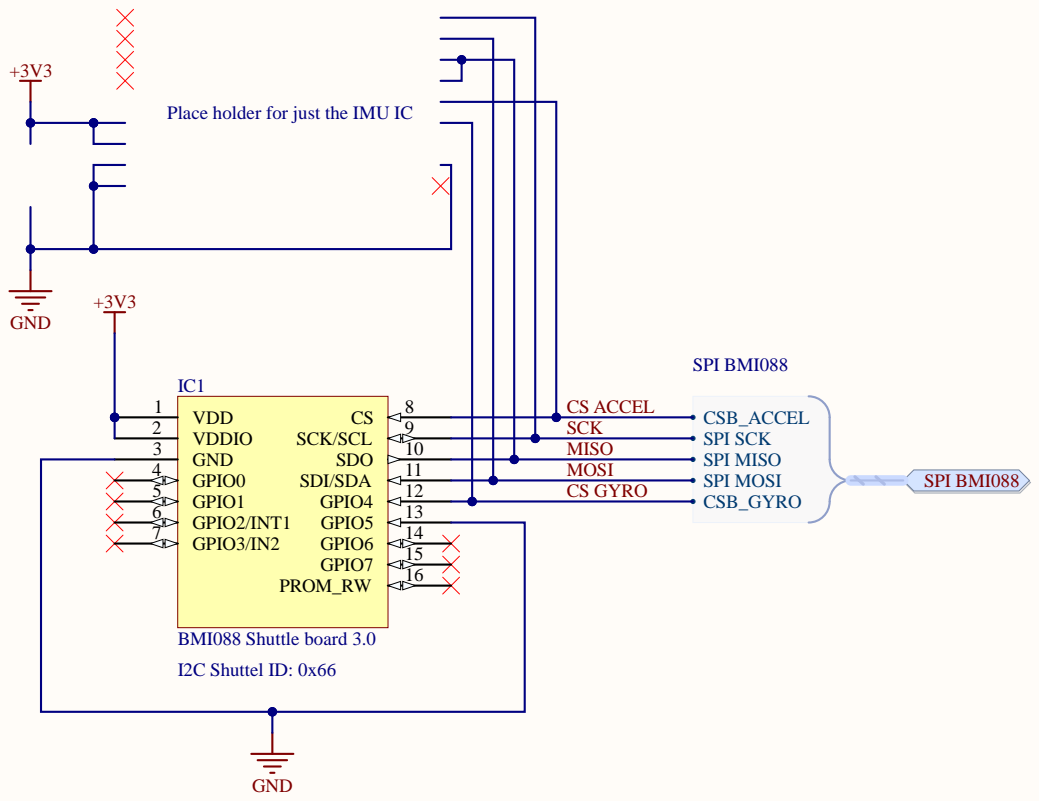
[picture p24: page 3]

Place holder for just the IMU I

CSB_ACCEL SPI SCK SPI MISO SPI MOSI

Project: CRS R C c a r

IMU-BMI088.SchDoc

C:\Users\Marcus\Documents\ETH\Altium SVN\CRS RC car v00P3\IMU-BMI088.SchDoc

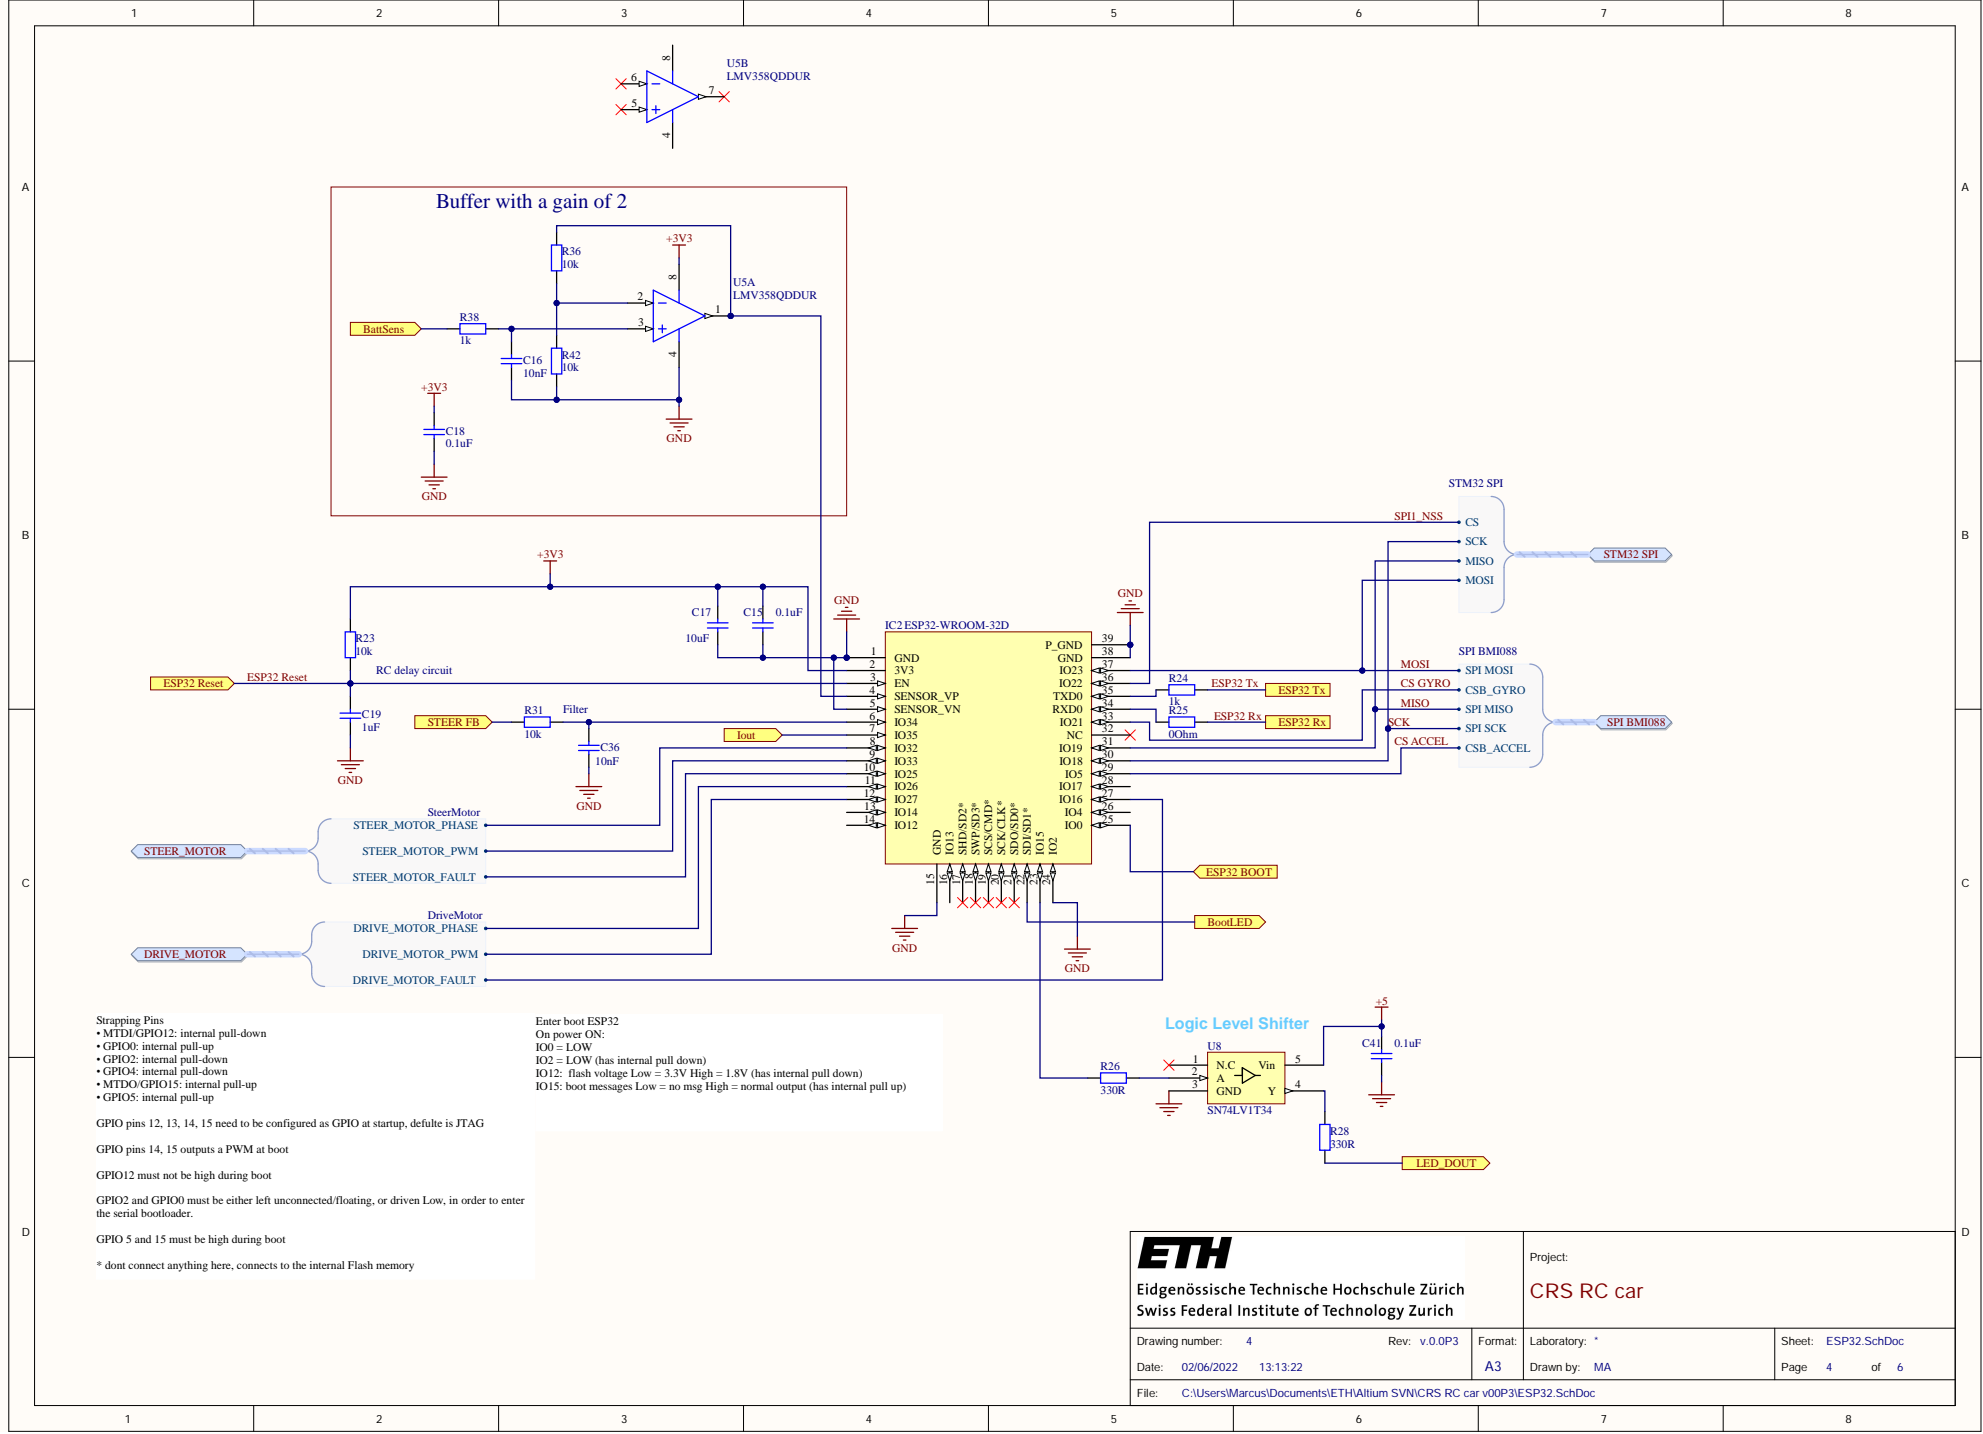
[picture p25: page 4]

Buffer with a gain of 2

MISO SCK

0Ohm | CS ACCEL

Strapping Pins
• MTDI/GPIO12: internal pull-down
• GPIO0: internal pull-up
• GPIO2: internal pull-down
• GPIO4: internal pull-down
• MTDO/GPIO15: internal pull-up
• GPIO5: internal pull-up

Enter boot ESP32
On power ON:
IO0 = LOW
IO2 = LOW (has internal pull down)
IO12: flash voltage Low = 3.3V High = 1.8V (has internal pull down)
IO15: boot messages Low = no msg High = normal output (has internal pull up)

GPIO pins 12, 13, 14, 15 need to be configured as GPIO at startup, defulte is JTAG

GPIO pins 14, 15 outputs a PWM at boot

GPIO12 must not be high during boot

GPIO2 and GPIO0 must be either left unconnected/floating, or driven Low, in order to enter
the serial bootloader.

GPIO 5 and 15 must be high during boot

Project: CRS RC car

* dont connect anything here, connects to the internal Flash memory

Drawing number: 4 | | Laboratory: * | ESP32.SchDoc Page 4 of 6

C:\Users\Marcus\Documents\ETH\Altium SVN\CRS RC car v00P3\ESP32.SchDoc

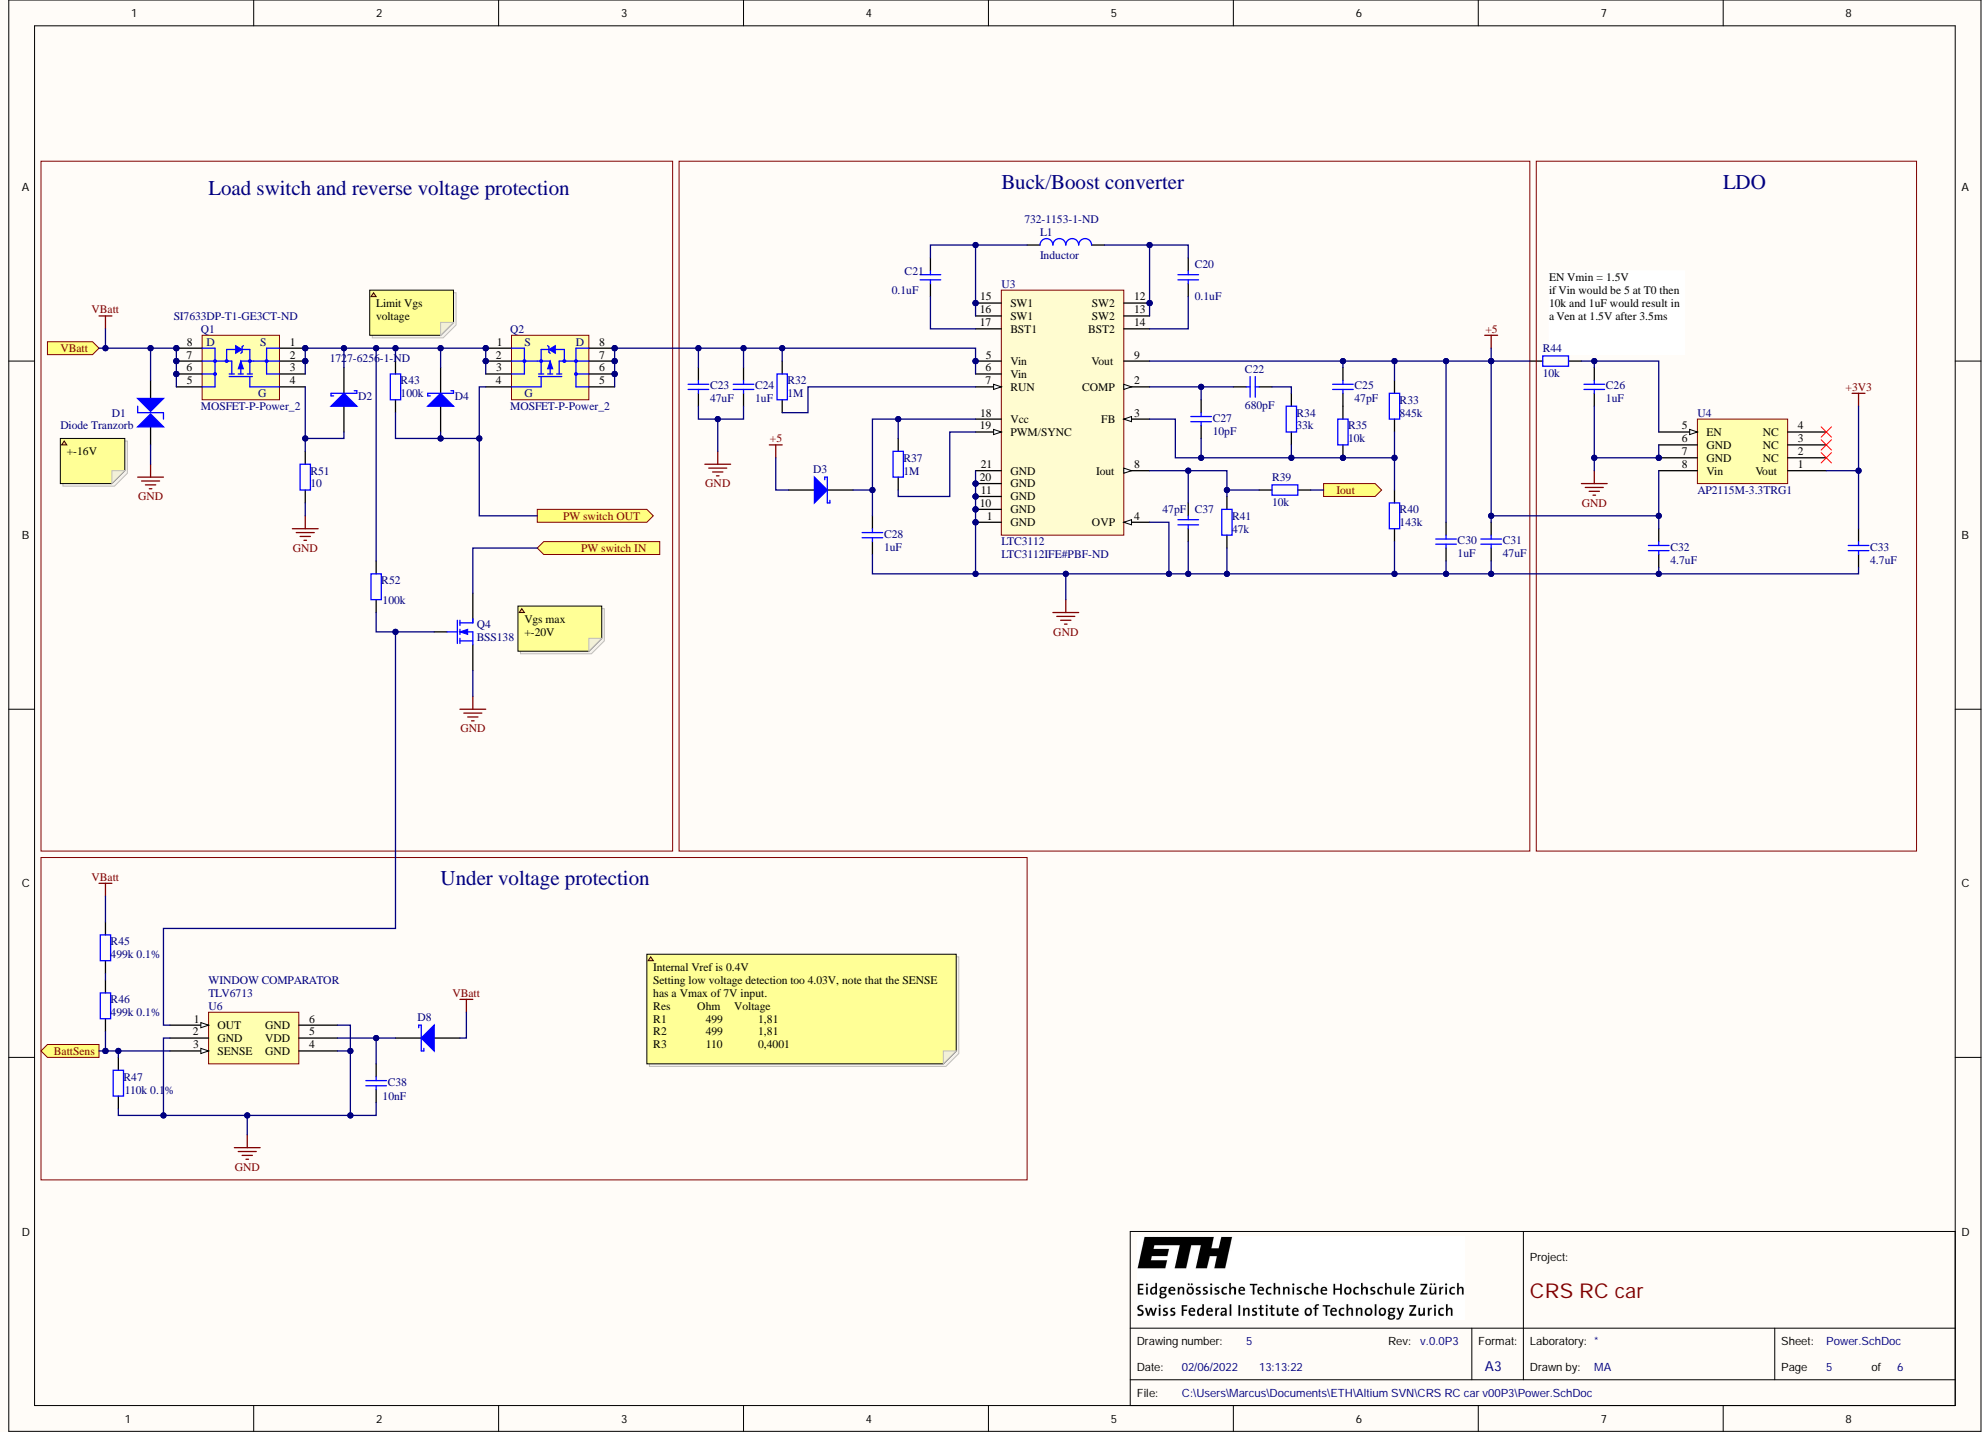
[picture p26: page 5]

Load switch and reverse voltage protection Limit Vgs VBatt | Buck/Boost converter 732-1153-1-ND L1 | LDO

EN Vmin = 1.5V
if Vin would be 5 at T0 then
10k and 1uF would result in
a Ven at 1.5V after 3.5ms

Internal Vref is 0.4V
Setting low voltage detection too 4.03V, note that the SENSE
has a Vmax of 7V input.

Project: CRS RC car

Power.SchDoc Page 5 of 6

C:\Users\Marcus\Documents\ETH\Altium SVN\CRS RC car v00P3\Power.SchDoc

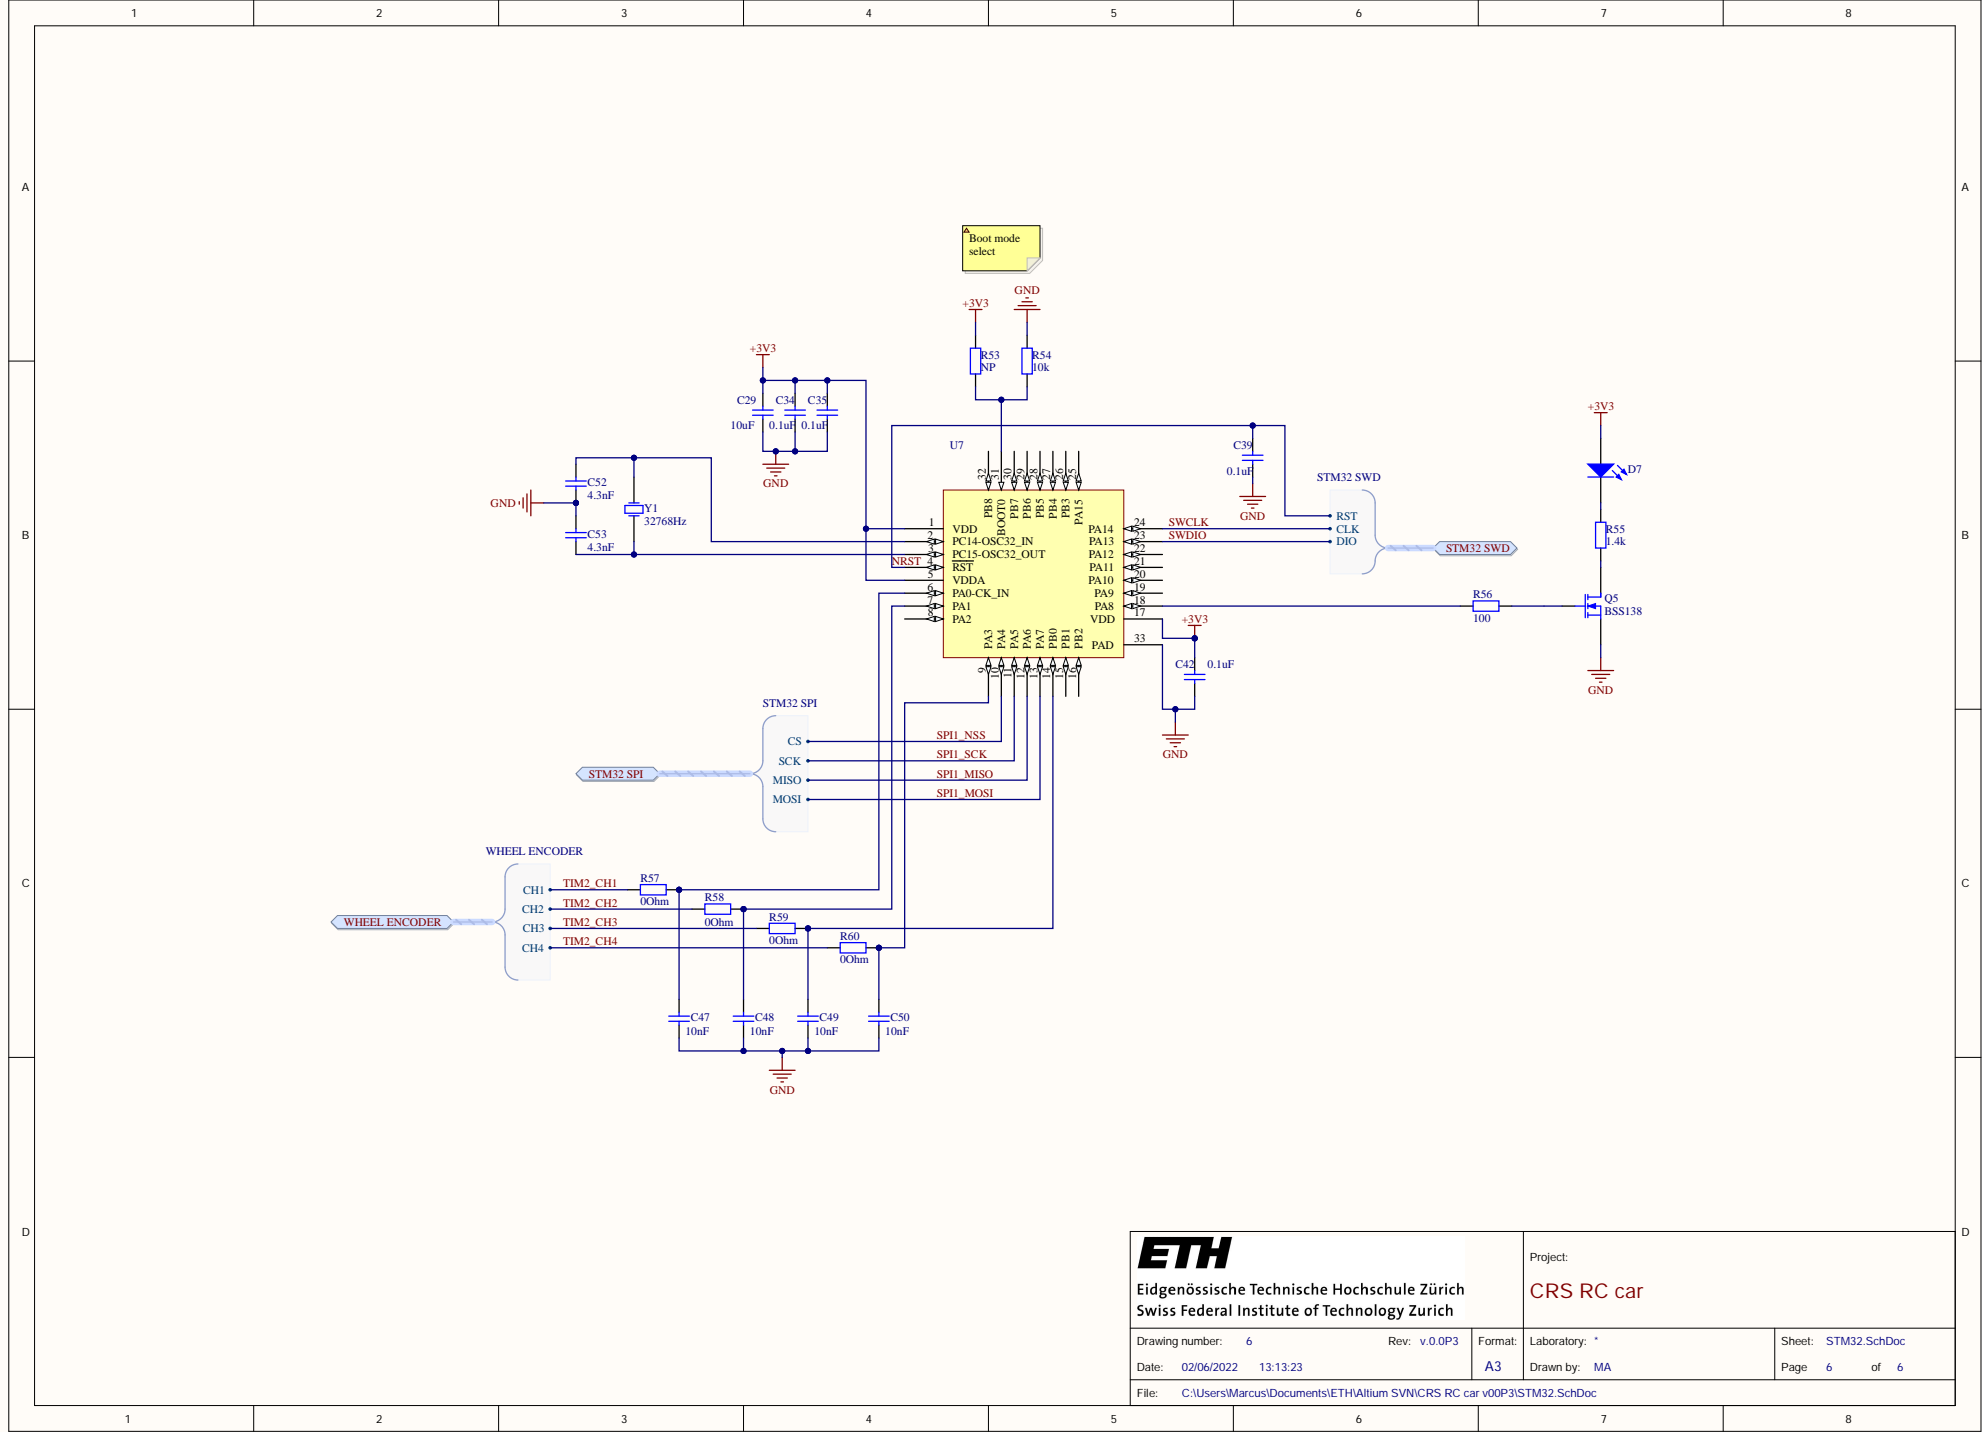
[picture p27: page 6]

PC14-OSC32_IN 2 | SWDIO
PC15-OSC32_OUT 3

NRST | RST 4

Project: CRS RC car

STM32.SchDoc Page 6 of 6

C:\Users\Marcus\Documents\ETH\Altium SVN\CRS RC car v00P3\STM32.SchDoc

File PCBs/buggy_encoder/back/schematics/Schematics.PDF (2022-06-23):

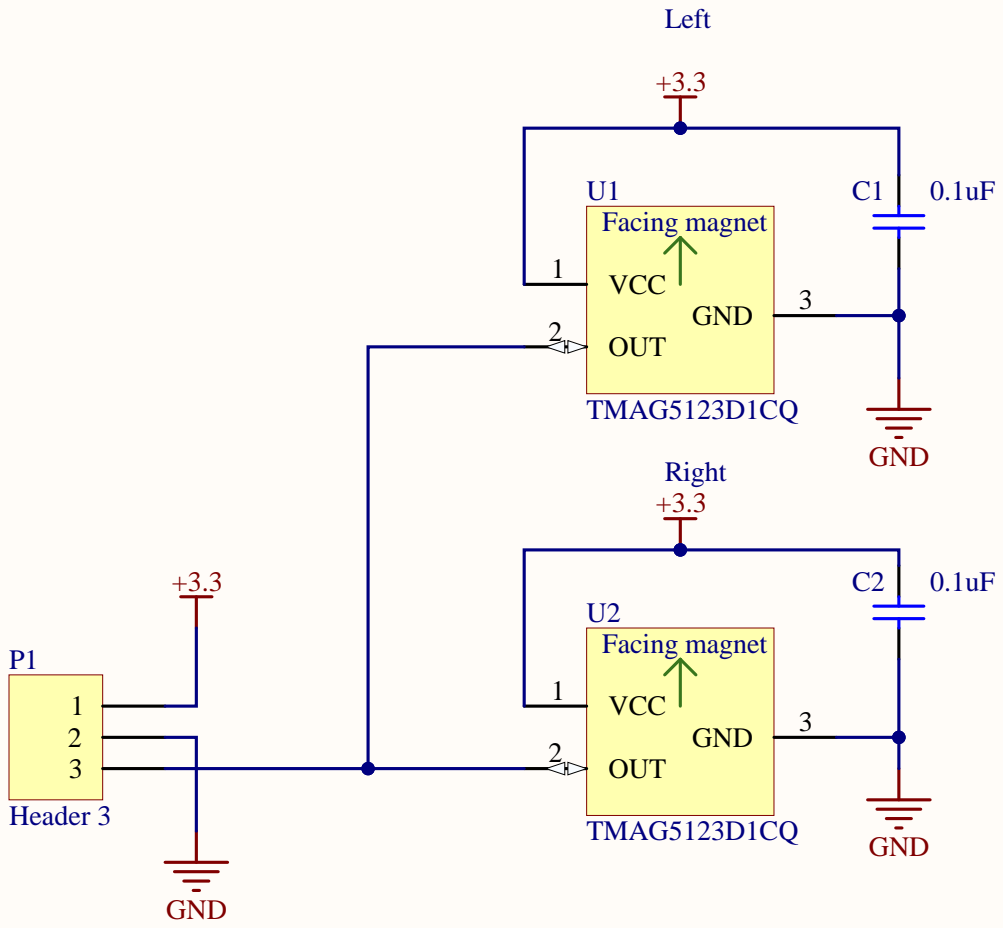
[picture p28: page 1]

Title:
CRS RC car front encoder

CRS RC car
C:\Users\Marcus\Documents\ETH\Altium SVN\CRS RC car back Encoder\Main.SchDoc




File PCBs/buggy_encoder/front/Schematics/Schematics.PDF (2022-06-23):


Title:
CRS RC car front encoder

CRS RC car
C:\Users\Marcus\Documents\ETH\Altium SVN\CRS RC car front Encoder\Main.SchDoc

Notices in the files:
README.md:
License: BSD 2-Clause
